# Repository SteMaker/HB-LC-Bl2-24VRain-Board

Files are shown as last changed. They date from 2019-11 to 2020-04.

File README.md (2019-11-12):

# HB-LC-Bl2-24VRain-Board
Selbstbau HomeMatic Hardware mit 2 Rolladenaktoren und Anschlussmöglichkeit eines 24V Regensensors

## Überblick
**Achtung: Ich übernehme keinerlei Verantwortung für die Sicherheit und Funktionsfähigkeit der Hardware wie auch der Firmware! Die Hardware verwendet Netzspannung 230V ist deshalb lebensgefährlich!**

Als Firmware verwende ich https://github.com/SteMaker/HB-LC-Bl2-RD.

Die Hardware unterstützt zwei Rolladenaktoren und entspricht im wesentlichen der Arbeit von Jérôme (https://github.com/jp112sdl) an https://github.com/jp112sdl/HM-LC-Bl1-FM-2.

Als Regensensor verwende ich einen Roto 24V Sensor mit Heizung (ich glaube ZEL STG RS 24V). Er bietet nur 3 Anschlussleitungen: 24V, GND, Regenindikation. Keine Möglichkeit die Heizung zu schalten.

Die Anwendung in meinem Fall ist es bis zu 2 Markisen anzusteuern und den in der Nähe befindlichen Regensensor gleich noch mit einzubinden.

## Dankeschön
Ein dickes, fettes Dankeschön an die homematic community sowas zu ermöglichen, insbesondere an pa-pa, Jérôme und Marco.

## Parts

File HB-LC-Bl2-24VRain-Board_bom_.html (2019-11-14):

Source File | /home/stefan/workspace/HB-LC-Bl2-24VRain-Board/HB-LC-Bl2-24VRain-Board.sch
BoM Date | Do 14 Nov 2019 14:10:07 CET
Schematic Version
Schematic Date
PCB Variant | [u'default']
KiCad Version | Eeschema 5.1.4-e60b266~84~ubuntu18.04.1
Component Groups | 19
Component Count (per PCB) | 47
Fitted Components (per PCB) | 47
Number of PCBs | 1
Total Component Count (for 1 PCBs) | 47
 | Description | Part | References | Value | Footprint | Quantity Per PCB | Datasheet | reichelt
1 | Unpolarized capacitor | C | C6 C7 C9 C10 | 100n | C_Rect_L4.6mm_W3.0mm_P2.50mm_MKS02_FKP02 | 4 | ~ | MKS02-63 100N
2 | Polarized capacitor | CP | C1 C2 | 10µF | CP_Radial_D5.0mm_P2.50mm | 2 | ~ | RAD 10/63
3 | Unpolarized capacitor | C | C3 C5 | 1u | C_Rect_L7.2mm_W5.5mm_P5.00mm_FKS2_FKP2_MKS2_MKP2 | 2 | ~ | MKS2-63 1,0u
4 | 100V 0.15A standard switching diode, DO-35 | 1N4148 | D1 D2 D3 D4 | 1N4148 | D_DO-35_SOD27_P2.54mm_Vertical_AnodeUp | 4 | http://www.nxp.com/documents/data_sheet/1N4148_1N4448.pdf | 1N 4148
5 | Fuse | Fuse | F1 | Fuse | Fuseholder_Cylinder-5x20mm_Schurter_FPG4_Vertical_Closed | 1 | ~ | PL FPG4-40
6 |  | ArduinoProMini | IC1 | ArduinoProMini | pro_mini | 1 | http://www.arduino.cc/en/uploads/Main/Arduino-Pro-Mini-schematic.pdf
7 | Generic connector, single row, 01x02, script generated (kicad-library-utils/schlib/autogen/connector/) | Conn_01x02_Female | J1 J5 J6 J7 | Motor_N | TerminalBlock_WAGO_236-102_1x02_P5.00mm_45Degree | 4 | ~ | WAGO 236-402
8 | Generic connector, single row, 01x03, script generated (kicad-library-utils/schlib/autogen/connector/) | Conn_01x03_Female | J2 J3 J4 | Taster Markise1 | TerminalBlock_WAGO_250-403_1x03_P2.50mm_45Degree | 3 | ~ | WAGO 250-403
9 | 24V, 5W, AC-DC module power supply, MeanWell | IRM-05-24 | PS1 | IRM-05-24 | Converter_ACDC_MeanWell_IRM-05-xx_THT | 1 | https://www.meanwell.com/Upload/PDF/IRM-05/IRM-05-SPEC.PDF | IRM-05-24
10 | 0.8A Ic, 45V Vce, NPN Transistor, TO-92 | BC337 | Q1 Q2 Q3 Q4 | BC337 | TO-92L_Wide | 4 | http://www.nxp.com/documents/data_sheet/BC817_BC817W_BC337.pdf | RND BC337
11 | Resistor | R | R1 R8 R9 R10 | 10k | R_Axial_DIN0204_L3.6mm_D1.6mm_P2.54mm_Vertical | 4 | ~ | 1/4W 10k
12 | Resistor | R | R7 | 1k | R_Axial_DIN0204_L3.6mm_D1.6mm_P2.54mm_Vertical | 1 | ~ | 1/4W 1,0K
13 | Resistor | R | R2 R3 R4 R5 | 2k4 | R_Axial_DIN0204_L3.6mm_D1.6mm_P2.54mm_Vertical | 4 | ~ | 1/4W 2k4
14 | Resistor | R | R11 R12 R13 R14 | 47 | R_Axial_DIN0204_L3.6mm_D1.6mm_P5.08mm_Vertical | 4 | ~ | 1/4W 47
15 | Resistor | R | R6 | 6k8 | R_Axial_DIN0204_L3.6mm_D1.6mm_P2.54mm_Vertical | 1 | ~ | 1/4W 6k8
16 |  | FINDER-40.61 | RL1 RL2 RL3 RL4 | FINDER-40.61 | FIN4061 | 4 |  | FIN 40.61.9 24V
17 | Push button switch, generic, two pins | SW_Push | SW1 | SW_Push | SW_PUSH_6mm_H4.3mm | 1 | ~ | TASTER 3301
18 |  | AM1S-xxxxS | U1 | AM1S-2403S | SIL-4 | 1 |  | SIM1-2403 SIL4
19 |  | CC1101 | U3 | CC1101-868MHz-Module | CC1101_Module | 1 | http://www.digirf.com/XWFU/2013/4f3751b81deca976.pdf

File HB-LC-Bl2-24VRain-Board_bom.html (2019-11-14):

Source File | /home/stefan/workspace/HB-LC-Bl2-24VRain-Board/HB-LC-Bl2-24VRain-Board.sch
BoM Date | Do 14 Nov 2019 13:35:47 CET
Schematic Version
Schematic Date
PCB Variant | [u'default']
KiCad Version | Eeschema 5.1.4-e60b266~84~ubuntu18.04.1
Component Groups | 17
Component Count (per PCB) | 49
Fitted Components (per PCB) | 49
Number of PCBs | 1
Total Component Count (for 1 PCBs) | 49
 | Description | Part | References | Value | Footprint | Quantity Per PCB | Datasheet | Bestellen | reichelt
1 | Unpolarized capacitor | C | C3 C4 C5 C6 C7 C8 C9 C10 | 100n | C_Rect_L4.6mm_W3.0mm_P2.50mm_MKS02_FKP02 | 8 | ~ | Nein
2 | Unpolarized capacitor | C | C1 C2 | 10µF | CP_Radial_D5.0mm_P2.50mm | 2 | ~ | nein
3 | 100V 0.15A standard switching diode, DO-35 | 1N4148 | D1 D2 D3 D4 | 1N4148 | D_DO-35_SOD27_P2.54mm_Vertical_AnodeUp | 4 | http://www.nxp.com/documents/data_sheet/1N4148_1N4448.pdf | Nein
4 | Fuse | Fuse | F1 | Fuse | Fuseholder_Cylinder-5x20mm_Schurter_FPG4_Vertical_Closed | 1 | ~ | Ja, reichelt | PL FPG4-40
5 |  | ArduinoProMini | IC1 | ArduinoProMini | pro_mini | 1 | http://www.arduino.cc/en/uploads/Main/Arduino-Pro-Mini-schematic.pdf
6 | Generic connector, single row, 01x02, script generated (kicad-library-utils/schlib/autogen/connector/) | Conn_01x02_Female | J1 J5 J6 J7 | Motor_N | TerminalBlock_WAGO_236-102_1x02_P5.00mm_45Degree | 4 | ~ | Ja, reichelt | WAGO 236-403 WAGO 236-402
7 | Generic connector, single row, 01x03, script generated (kicad-library-utils/schlib/autogen/connector/) | Conn_01x03_Female | J2 J3 J4 | Taster Markise1 | TerminalBlock_WAGO_250-403_1x03_P2.50mm_45Degree | 3 | ~
8 | 24V, 5W, AC-DC module power supply, MeanWell | IRM-05-24 | PS1 | IRM-05-24 | Converter_ACDC_MeanWell_IRM-05-xx_THT | 1 | https://www.meanwell.com/Upload/PDF/IRM-05/IRM-05-SPEC.PDF |  | IRM-05-24
9 | 0.8A Ic, 45V Vce, NPN Transistor, TO-92 | BC337 | Q1 Q2 Q3 Q4 | BC337 | TO-92L_Wide | 4 | http://www.nxp.com/documents/data_sheet/BC817_BC817W_BC337.pdf | Ja, reichelt | RND BC337
10 | Resistor | R | R1 R2 R3 R4 R5 R8 R9 R10 | 10k | R_Axial_DIN0204_L3.6mm_D1.6mm_P2.54mm_Vertical | 8 | ~ | Ja, reichelt Nein | 1/4W 68k
11 | Resistor | R | R7 | 1k | R_Axial_DIN0204_L3.6mm_D1.6mm_P2.54mm_Vertical | 1 | ~ | Nein
12 | Resistor | R | R11 R12 R13 R14 | 47 | R_Axial_DIN0204_L3.6mm_D1.6mm_P5.08mm_Vertical | 4 | ~ | Ja, reichelt | 1/4W 68k
13 | Resistor | R | R6 | 6k8 | R_Axial_DIN0204_L3.6mm_D1.6mm_P2.54mm_Vertical | 1 | ~ | Ja, reichelt | 1/4W 68k
14 |  | FINDER-40.61 | RL1 RL2 RL3 RL4 | FINDER-40.61 | FIN4061 | 4 |  |  | FIN 40.61.9 24V
15 | Push button switch, generic, two pins | SW_Push | SW1 | SW_Push | SW_PUSH_6mm_H4.3mm | 1 | ~ | Ja, reichelt | TASTER 3301
16 |  | AM1S-xxxxS | U1 | AM1S-2403S | SIL-4 | 1 |  |  | SIM1-2403 SIL4
17 |  | CC1101 | U3 | CC1101-868MHz-Module | CC1101_Module | 1 | http://www.digirf.com/XWFU/2013/4f3751b81deca976.pdf | Nein

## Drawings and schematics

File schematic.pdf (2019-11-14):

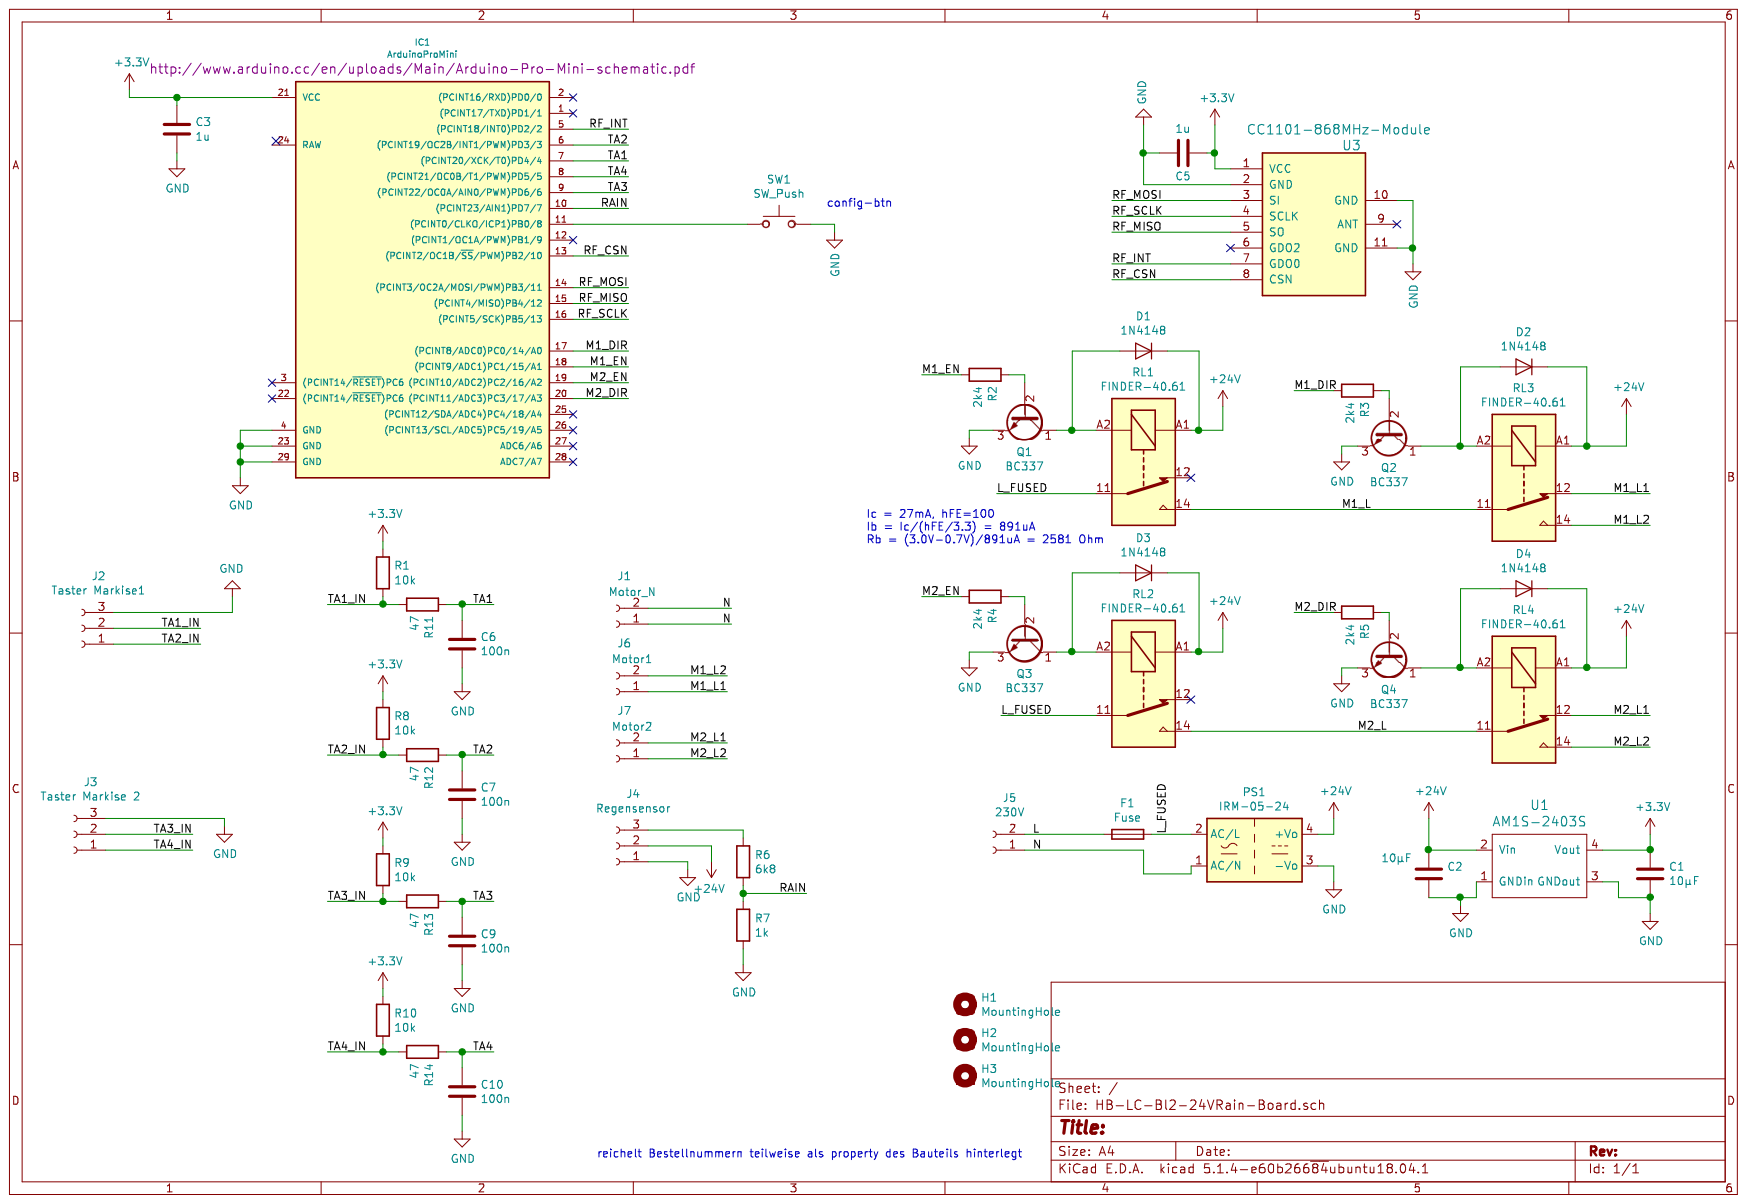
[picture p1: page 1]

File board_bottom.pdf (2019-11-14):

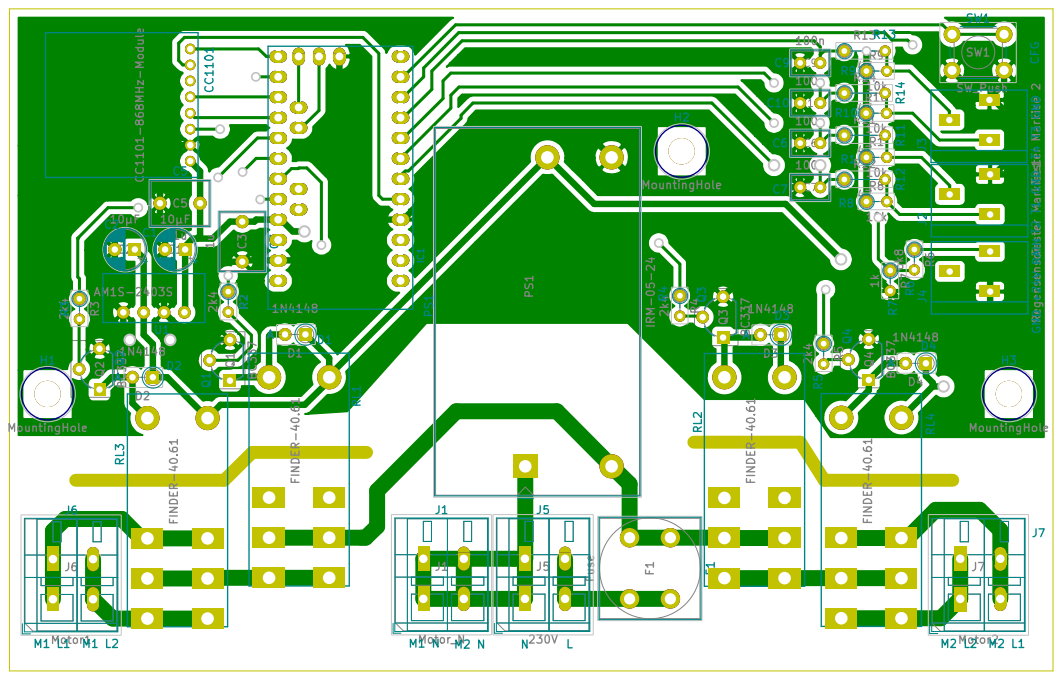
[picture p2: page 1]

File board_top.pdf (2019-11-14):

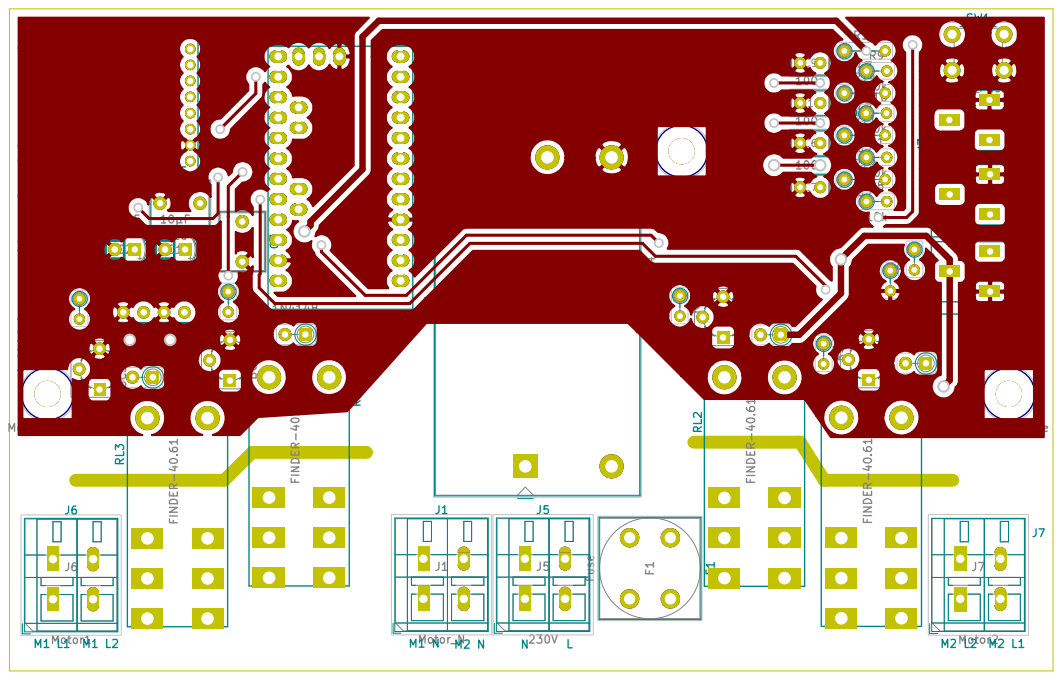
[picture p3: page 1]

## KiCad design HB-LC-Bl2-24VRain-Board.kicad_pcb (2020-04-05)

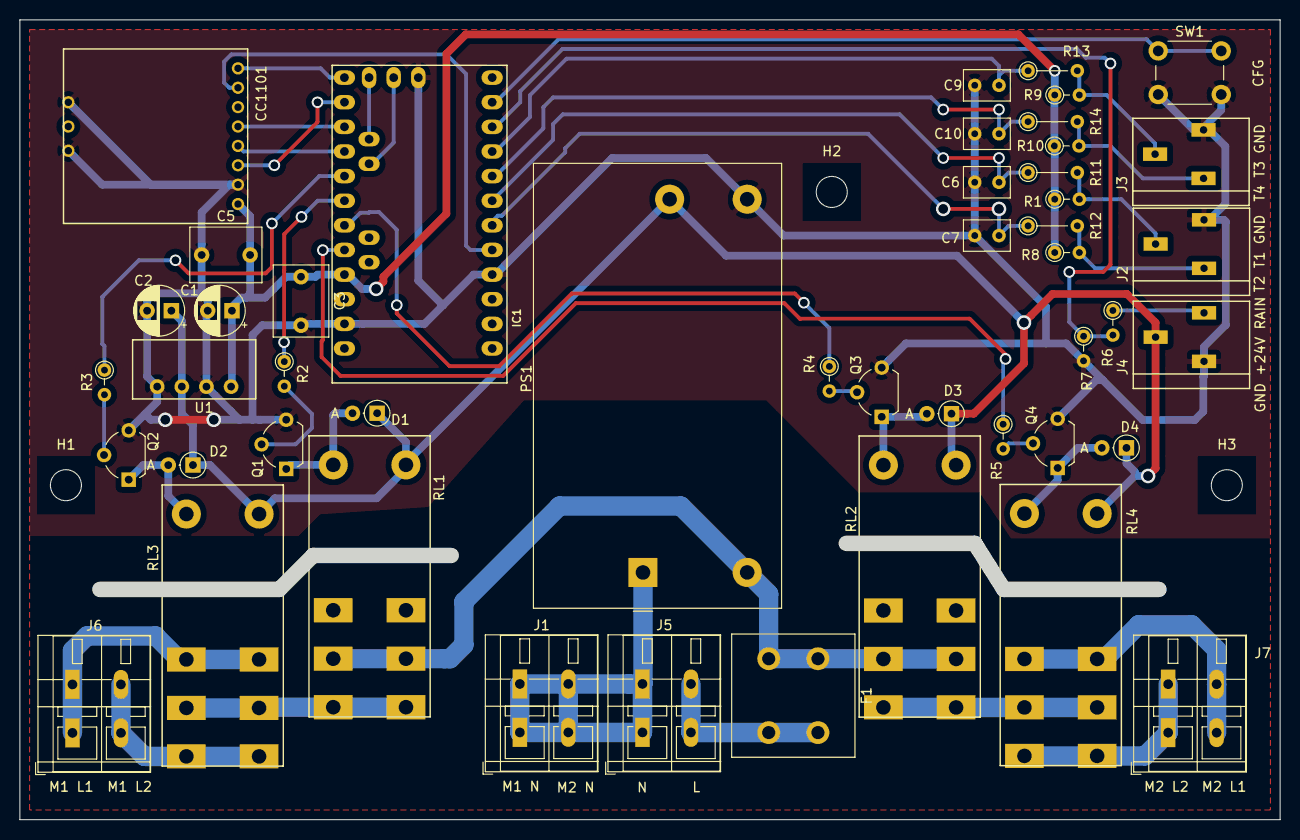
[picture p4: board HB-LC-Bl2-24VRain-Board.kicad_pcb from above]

Board: 2 copper layers, 130.0 x 82.5 mm, 50 parts (0 on the bottom side), 42 nets.

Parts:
C1, C2: 10µF; CP_Radial_D5.0mm_P2.50mm
C3, C5: 1u; C_Rect_L7.2mm_W5.5mm_P5.00mm_FKS2_FKP2_MKS2_MKP2
C6, C7, C9, C10: 100n; C_Rect_L4.6mm_W3.0mm_P2.50mm_MKS02_FKP02
D1, D2, D3, D4: 1N4148; D_DO-35_SOD27_P2.54mm_Vertical_AnodeUp
F1: Fuse; Fuseholder_Cylinder-5x20mm_Schurter_FPG4_Vertical_Closed
H1, H2, H3: MountingHole; MountingHole_3.2mm_M3
IC1: ArduinoProMini; pro_mini
J1: Motor_N; TerminalBlock_WAGO_236-102_1x02_P5.00mm_45Degree
J2: Taster Markise1; TerminalBlock_WAGO_250-403_1x03_P2.50mm_45Degree
J3: Taster Markise 2; TerminalBlock_WAGO_250-403_1x03_P2.50mm_45Degree
J4: Regensensor; TerminalBlock_WAGO_250-403_1x03_P2.50mm_45Degree
J5: 230V; TerminalBlock_WAGO_236-102_1x02_P5.00mm_45Degree
J6: Motor1; TerminalBlock_WAGO_236-102_1x02_P5.00mm_45Degree
J7: Motor2; TerminalBlock_WAGO_236-102_1x02_P5.00mm_45Degree
PS1: IRM-05-24; Converter_ACDC_MeanWell_IRM-05-xx_THT
Q1, Q2, Q3, Q4: BC337; TO-92L_Wide
R1, R8, R9, R10: 10k; R_Axial_DIN0204_L3.6mm_D1.6mm_P2.54mm_Vertical
R2, R3, R4, R5: 2k4; R_Axial_DIN0204_L3.6mm_D1.6mm_P2.54mm_Vertical
R6: 6k8; R_Axial_DIN0204_L3.6mm_D1.6mm_P2.54mm_Vertical
R7: 1k; R_Axial_DIN0204_L3.6mm_D1.6mm_P2.54mm_Vertical
R11, R12, R13, R14: 47; R_Axial_DIN0204_L3.6mm_D1.6mm_P5.08mm_Vertical
RL1, RL2, RL3, RL4: FINDER-40.61; FIN4061
SW1: SW_Push; SW_PUSH_6mm_H4.3mm
U1: AM1S-2403S; SIL-4
U3: CC1101-868MHz-Module; CC1101_Module

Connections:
+3V3: C1.1, C3.1, C5.2, IC1.21, R1.1, R8.1, R9.1, R10.1, U1.4, U3.1
+24V: C2.1, D1.1, D2.1, D3.1, D4.1, J4.2, PS1.4, RL1.A1, RL2.A1, RL3.A1, RL4.A1, U1.2
/L: F1.2, J5.2
/L_FUSED: F1.1, PS1.2, RL1.11, RL1.21, RL2.11, RL2.21
/M1_DIR: IC1.17, R3.1
/M1_EN: IC1.18, R2.1
/M1_L: RL1.14, RL1.24, RL3.11, RL3.21
/M1_L1: J6.1, RL3.12, RL3.22
/M1_L2: J6.2, RL3.14, RL3.24
/M2_DIR: IC1.20, R5.1
/M2_EN: IC1.19, R4.1
/M2_L: RL2.14, RL2.24, RL4.11, RL4.21
/M2_L1: J7.2, RL4.12, RL4.22
/M2_L2: J7.1, RL4.14, RL4.24
/N: J1.1, J1.2, J5.1, PS1.1
/RAIN: IC1.10, R6.2, R7.1
/RF_CSN: IC1.13, U3.8
/RF_INT: IC1.5, U3.7
/RF_MISO: IC1.15, U3.5
/RF_MOSI: IC1.14, U3.3
/RF_SCLK: IC1.16, U3.4
/TA1: C6.1, IC1.7, R11.1
/TA1_IN: J2.2, R1.2, R11.2
/TA2: C7.1, IC1.6, R12.1
/TA2_IN: J2.1, R8.2, R12.2
/TA3: C9.1, IC1.9, R13.1
/TA3_IN: J3.2, R9.2, R13.2
/TA4: C10.1, IC1.8, R14.1
/TA4_IN: J3.1, R10.2, R14.2
GND: C1.2, C2.2, C3.2, C5.1, C6.2, C7.2, C9.2, C10.2, IC1.4, IC1.23, IC1.29, J2.3, J3.3, J4.1, PS1.3, Q1.3, Q2.3, Q3.3, Q4.3, R7.2, SW1.2, U1.1, U1.3, U3.2, U3.10, U3.11
unnamed: D1.2, Q1.1, RL1.A2
unnamed: D2.2, Q2.1, RL3.A2
unnamed: D3.2, Q3.1, RL2.A2
unnamed: D4.2, Q4.1, RL4.A2
unnamed: IC1.11, SW1.1
unnamed: J4.3, R6.1
unnamed: Q1.2, R2.2
unnamed: Q2.2, R3.2
unnamed: Q3.2, R4.2
unnamed: Q4.2, R5.2
unnamed: RL1.12, RL1.22
unnamed: RL2.12, RL2.22

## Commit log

2019-11-09 Initial commit - version 0.9
    [HB-LC-Bl2-24VRain-Board.kicad_pcb, HB-LC-Bl2-24VRain-Board.sch]
2019-11-12 Several schematic updates
    [HB-LC-Bl2-24VRain-Board.kicad_pcb, HB-LC-Bl2-24VRain-Board.sch]
2019-11-13 Few updates to layout. But not yet done.
    [HB-LC-Bl2-24VRain-Board.kicad_pcb]
2019-11-13 Version 1.0
    - Some beautifications done
    - Replaced 2x100nF at CC1101 at Arduino woth 1uF each
    - Fixed the base resistor for the relay control
    [HB-LC-Bl2-24VRain-Board.kicad_pcb, HB-LC-Bl2-24VRain-Board.sch]
2019-11-13 Added schematic and layouts as pdf
2019-11-14 Adding BOM, not finished
    [HB-LC-Bl2-24VRain-Board.sch]
2019-11-14 Added the BOM to a new file
    [HB-LC-Bl2-24VRain-Board.sch]
2020-04-05 Added missing GND connections of CC101
    [HB-LC-Bl2-24VRain-Board.kicad_pcb]
